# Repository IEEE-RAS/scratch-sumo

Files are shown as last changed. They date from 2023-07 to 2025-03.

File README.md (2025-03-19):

# Scratch Sumo

O scratch sumo é um projeto educacional para ensino de pensamento computacional e robótica usando linguagem de programação em bloco, como implementado por ferramentas como Scratch ou Google Blockly.
Consiste em 2 robôs-sumô que serão programados pelos estudantes e competem entre si num jogo simplificado.

## Materiais

- 2x Arduino NANO
- 2x MT3806 Step-up
- 2x USB Micro LiIon BMS
- 4x N20 Motor Reduzido
- 2x HC-SR04 Sensor Ultrassonico
- 4x Sensor Obstáculo Reflexivo IR
- 2x Ponte H L9110s
- 2x Buck Converter LM2596

O chassis é confectionado em plástico (majoritariamente ABS) e produzido por impressão 3D.

## Snapshot

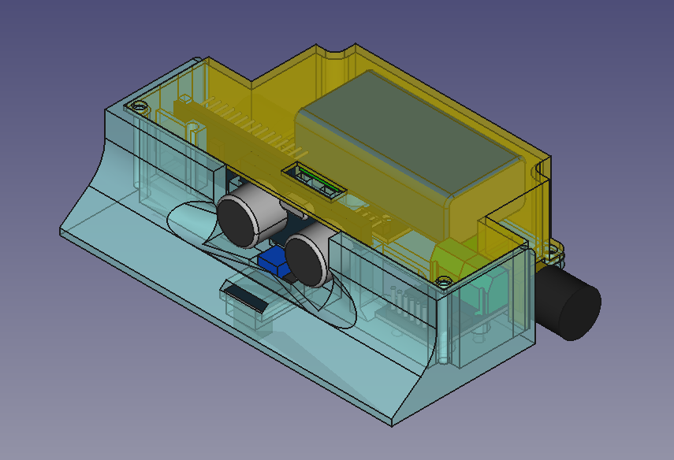
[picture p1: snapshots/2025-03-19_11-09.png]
Prototipo


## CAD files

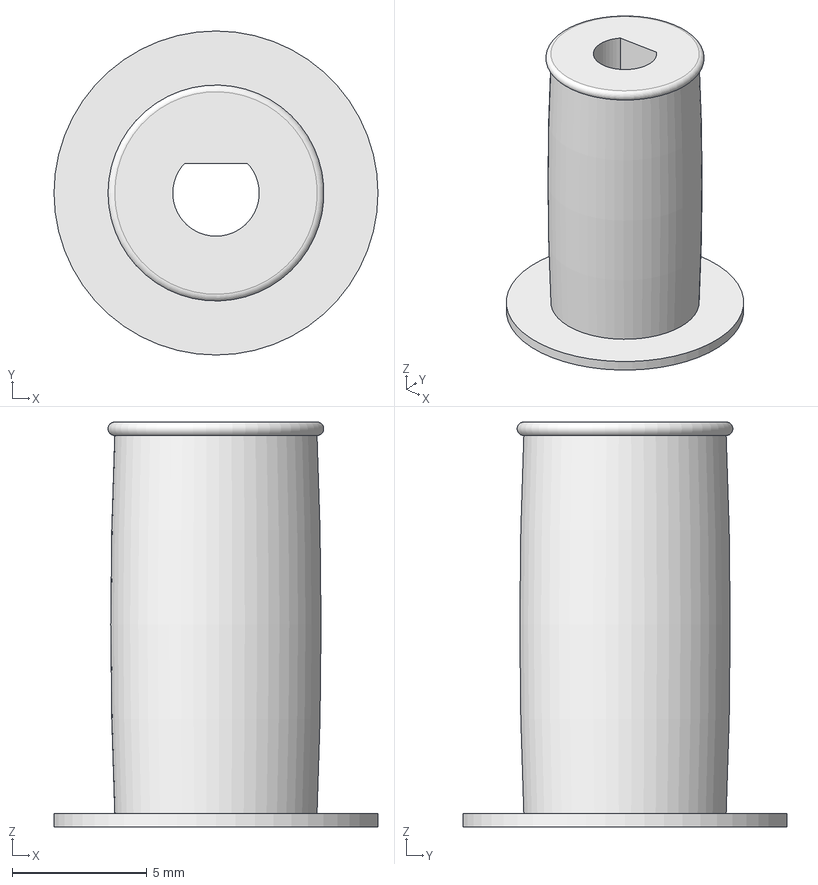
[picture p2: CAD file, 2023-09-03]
model/hub_roda.FCStd
12.0 x 12.0 x 15.0 mm

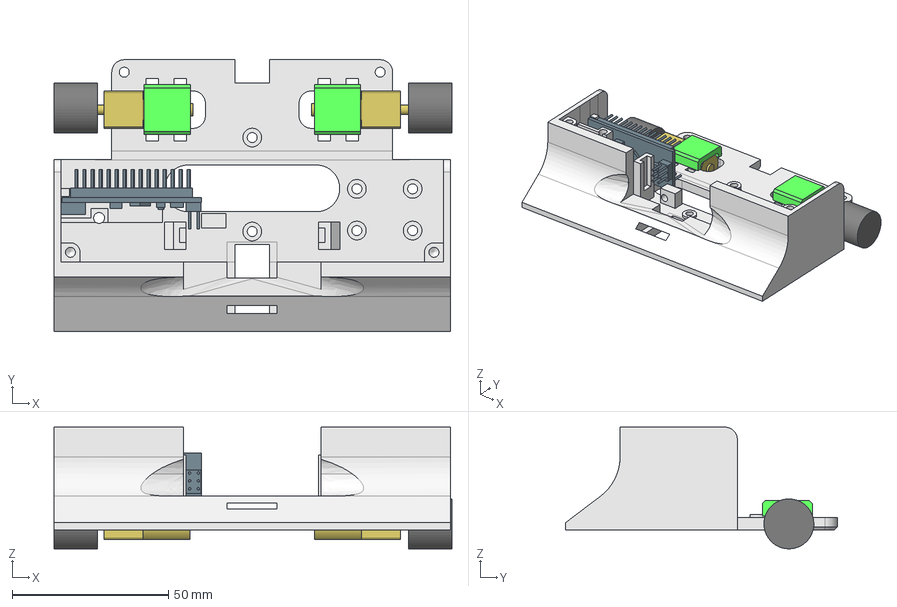
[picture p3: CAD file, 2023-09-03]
model/sumoV1.FCStd
127.5 x 87.0 x 39.0 mm
motor_support001
motor002
roda1
roda2
motor001
motor_support002
testbed001
nano

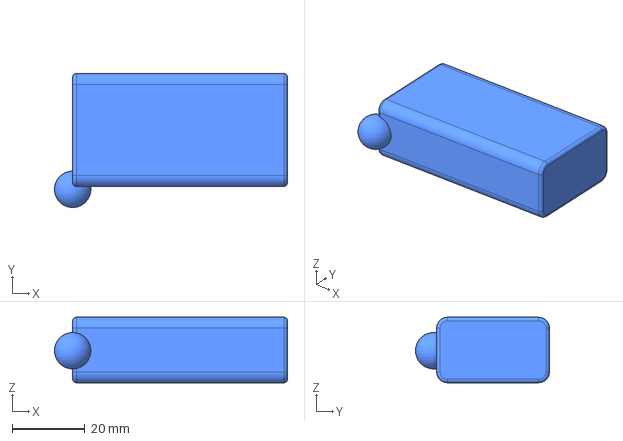
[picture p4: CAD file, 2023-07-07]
model/batteryPack.FCStd
64.0 x 36.8 x 18.0 mm

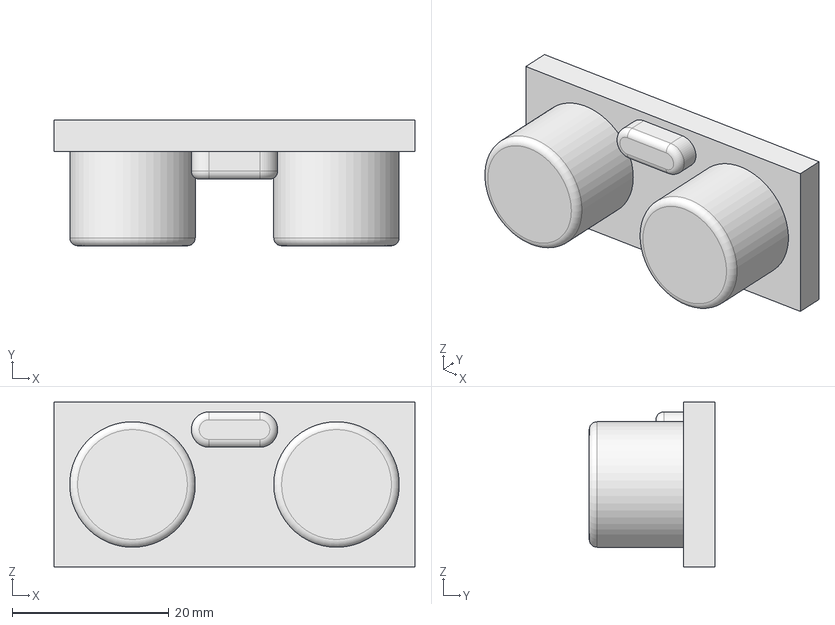
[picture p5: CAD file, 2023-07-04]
model/HC-SR04.FCStd
46.0 x 16.0 x 21.0 mm

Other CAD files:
model/HC-SR04-Body.stl

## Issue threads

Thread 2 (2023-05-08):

Modelagem Chassis

ShinJaca, 2023-05-08:
# Modelagem Chassis

O chassis do robo sumo será baseado no chassis desenvolvido para o seguidor de linha versão 2, feito em impressão 3D, é compacto e leve. Deverá também abrigar os sensores, baterias e placas de controle de forma "monolítica", além da pá frontal, característica de robôs sumô.

## Modificações necessárias

- Pá frontal: deve ter espaço para os sensores de ultrassom e infravermelho
- Espaço para roda: as rodas do robô sumô são maiores que as rodas do seguidor de linha, esse espaço deverá ser criado no layout do chassis.

ShinJaca, 2023-07-07:
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

Closed 2023-09-13.

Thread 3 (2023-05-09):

Teste de Baterias

Fernanda-Marinho, 2023-05-09:
3 baterias foram testadas:

- Uma pegou 3.8V, abaixou pra 3.7 e manteve
- Uma pegou 3.8V, abaixou pra 3.6, não acho que está mto boa
- Outra carregou bastante (não esperei o carregador apitar), mas pegou 3.9V

* Temos que ver se o carregador é programável.

victorcsar, 2023-05-11:
+2 baterias testadas:

- As duas vermelhas não passaram de 4.1V
- Ao retirar as duas descarregaram bem rápido e estabilizaram em 3.8

- Temos que verificar novamente se todas estão segurando a carga.

victorcsar, 2023-05-11:
Ainda tem mais de 15 baterias para testar, é o tempo de carregamento esta em torno de 64 min para cada. Nesse ritmo não sera possível testar todas no período de uma semana.

victorcsar, 2023-05-11:
seria interessante utilizar o seguidor de linha para verificar como será o comportamento das baterias ja carregadas, ou utilizar outro robô que esteja funcionando.

victorcsar, 2023-05-11:
[](https://www.youtube.com/watch?v=21b8qLPA_-M&ab_channel=JALASCKARC)

Video de como carregar as baterias, como o carregador é um pouco de ferente, tive que converter v para mah. As baterias pegam 3.6v segundo pesquisei, então aumentei no carregador para 3600 mah. Irei carregar uma para ve se muda alguma coisa.

Fernanda-Marinho, 2023-05-11:
Mais uma bateria foi carregada hoje (11/05), ficou com 3.9V

Fernanda-Marinho, 2023-05-11:
Mais uma bateria carrregada, com 3.8V. Ao todo, hj (11/05) temos 8 baterias carregadas: todas entre 3.6 e 3.9 V

Fernanda-Marinho, 2023-05-15:
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

Essa bateria tá marcando 3.7V, mas durante o carregamento esquentou muito, tirei com 2h de carregamento.
O carregador tá apitando bateria baixa pra as baterias com 2.0V e 2.3V
Ele foi programado pra só carregar acima de 2.4V?

Fernanda-Marinho, 2023-05-15:
Conferi a bateria que estava esquentando, já ta fria porém baixou de 4.0V para 3.8V
Mais duas baterias (das cinzas) foram carregadas (sem superaquecimento) e ficaram em 4.0V

Fernanda-Marinho, 2023-05-16:
Ao todo, temos 15 baterias  carregadas: entre 3.6V e 4.0V

victorcsar, 2023-05-17:
https://www.youtube.com/watch?v=uchFUiXPdQU&ab_channel=noteb00kpc
Esse video mostra como resolver o problema de low battery, tem uma opçao no carreador para chegar a bateria, deixa uns minutos depois da stop e coloca para carregar. O video carrega uma bateria de LIPo mas funciona para as de Lition.

victorcsar, 2023-05-17:
+1 bateria carregada, demorou 110 min e estava com 2v,  agora pegou 3.9V

Fernanda-Marinho, 2023-05-25:
Todas as baterias foram carregadas. Estamos começando a testar a duração delas no seguidor de linha

Fernanda-Marinho, 2023-05-25:
Uma bateria foi testada no seguidor de linha. Durou 40min porém foi de 3.8V para 3.7V
Eu acho que o seguidor de linha possa estar com mal contato ou algum bug. Um dos sensores do seguidor (S5) não ta funcionando

Fernanda-Marinho, 2023-05-26:
Precisa ver como funciona a função de descarregar a bateria. Pois muito provável que ela dê um valor em Mah e aí olhando quanto a bateria tem (de fábrica) dá pra ter uma noção de quantos por cento de carga ela tem. Se tiver uns 80% de carga ainda, ta boa.

Fernanda-Marinho, 2023-05-26:
https://pdf1.alldatasheet.com/datasheet-pdf/view/597041/PANASONICBATTERY/NCR18650.html (datasheet de uma das baterias testadas no seguidor de linha), vem com capacidade de fábrica de 2900mAh
Ela vai do max 4.2V (no carregamento)
E min de 2.5V (no descarregamento) pelo q eu entendi. Se tiver errado olhem o pdf e me corrijam

Closed 2023-07-04.

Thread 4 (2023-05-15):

Teste dos sensores

Fernanda-Marinho, 2023-05-15:

Fernanda-Marinho, 2023-05-15:
Quais sensores serão testados? Precisamos separar esses sensores e deixar reservado. Até o momento eu só sei do sonar.

ShinJaca, 2023-07-12:
Sensores:
- [x] TCRT5000 sensor IR
- [ ] HC-SR04 sensor ultrassom

ShinJaca, 2023-07-13:
## Atualização

Um teste mais extenso com 2 sensores ultrassonicos realizados um contra o outro demonstrou que os sensores afastados a partir de cerca de 15cm interferem e corrompem as medidas um do outro

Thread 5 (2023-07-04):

Função Blockly@rduino

ShinJaca, 2023-07-04:
# Funções a implementar

**Movimento**:
- andar pra frente
- andar pra tras
- andar pra frente e esquerda
- andar à frente e direita
- andar à tras esquerda
- andar à tras direta

**Sensores**:
- Ler distância sensor ultrassom
- ler detecção de borda (sensor IR)

Fernanda-Marinho, 2023-07-11:
Documentação blockly -> https://developers.google.com/blockly?hl=pt-br&authuser=0
Projeto blockly@rduino ->
Código-fonte (a ideia é fazer um fork e ir modificando conforme nossas necessidades) -> https://github.com/technologiescollege/Blockly-at-rduino

Fernanda-Marinho, 2023-07-11:
Achei o código que gera o "Blockly.Arduino", está dentro da pasta "generation". Lá ele contém as funções que traduz o que é Blockly para arduino.
Tem funções também que adiciona os includes, incializa código e verifica variáveis.

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

ShinJaca, 2023-07-20:
## Rodando localmente

Para rodar localmente usei o método de container com docker, para tanto é interessante criar o arquivo Dockerfile no raiz do repositório do Blockly@rduino contendo a diretiva:
```dockerfile
FROM httpd:2.4
```
em seguida, estando no repositório, construir a imagem ( necessário toda vez que algumas alterações são feitas ):
```bash
docker build -t apache2-server .
```
ao finalizar, iniciar um container com a imagem criada:
```bash
docker run -dit --name blocklyarduino -p 8080:80 --mount type=bind,src=.,dst=/usr/local/apache2/htdocs apache2-server
```
e acessando a aplicação pelo navegador através do endereço localhost:8080 ( nesse caso a porta encaminhada foi 8080, mas pode ser a de preferência ).

ShinJaca, 2023-07-20:
## Criando uma biblioteca

A aplicação usa basicamente 5 arquivos para configurar uma biblioteca:
- toolbox/toolbox_arduino_1.xml ( ou outro nível )
- lang/pt-br.js ( e outras traduções )
- blocks/arduino_resume.js ( contém a chamada para as definições de bloco )
- blocks/fabricante/fabricante.js ( substituindo o fabricante pelo nome da biblioteca, definições de bloco )
- generators/arduino_resume.js ( chamada para as definições do gerador de codigo )
- generators/fabricante.js (definições dos geradores )

### Toolbox

A toolbox, ou caixa de ferramentas agrupa os blocos disponíveis para o projeto, nesse caso é pensado para servir de agrupamento por nível de dificuldade, mais ou menos abstrato.
Aqui são listados os blocos que aparecem para o usuário:
```xml
<category name="CAT_NOME" colour="#6D0194">
	<block type="fabricante_nome_do_bloco"></block>
        <block type="fabricante_outro_bloco"></block>
</category>
```

### Traduções

Para que a biblioteca apareça na listagem do nível selecionado, uma tradução para ela deve ser criada nos arquivos de traduções da pasta `lang/BlocklyArduino_blocks`, numa propriedade específica para a biblioteca (categoria), como segue:
```js
Blockly.Msg.CAT_NOME = "Nome da Biblioteca";
```
### TODO
- resumes
- blocks
- generators

ShinJaca, 2023-07-20:
# Funções de teste

Três funções de teste foram implementadas `moveFrente`, `moveTras` e `parar`, para fazer funcionar, é necessário mesclar os arquivos de configuração e copiar os arquivos de definição de blocos e gerador na sua copia do Blockly@rduino.

Closed 2023-08-07.

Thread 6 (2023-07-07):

Funções Arduino

ShinJaca, 2023-07-07:
# Funções Arduino

Desenvolvimento das funções necessárias para funcionamento do robô ( codigo em linguagem para o arduino )

**Funções de movimento:**
- seguir em frente
- seguir à tras
- à frente e esquerda
- à frente e direita
- tras e esquerda
- tras e direita
- parar

**Funções de sensores**:
- ler sensor de distância ( Ultrassom )
- ler sensores de borda ( IR )

ShinJaca, 2023-07-13:
## Modulo ponte H
O nosso modulo de ponte H não provém pino de enable, sendo necessário modular um dos pinos de controle de direção para produzir o efeito de controle de rotação dos motores, assim também economizando 2 pinos. mas exigindo agora que os pinos de controle sejam todos pinos com PWM 🥲.

Closed 2023-08-17.

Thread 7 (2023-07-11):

Impressão prototipo

ShinJaca, 2023-07-11:
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

ShinJaca, 2023-07-11:
Primeiro protótipo:
- pinos posicionamento para driver de motor
- pinos posicionamento para sensores IR
- suporte para sensor ultrassom
- slot para sensor ultrassom
- slots para sensores IR

Closed 2023-07-11.

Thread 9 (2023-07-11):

Testes de Movimento

ShinJaca, 2023-07-11:

ShinJaca, 2023-07-20:
## Movimentos
Foram realizados testes de movimento com avanço, retrocesso e curvas, mas aparentemente existe um problema com constância de um dos motores, aparentemente a frequência de PWM do pino escolhido pode estar influenciando na rotação e causando instabilidades.

Closed 2023-08-07.

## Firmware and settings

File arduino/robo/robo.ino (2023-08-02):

// Código de referência em: https://blog.arduinoomega.com/robo-autonomo-basico-com-sensor-ultrassonico-hc-sr04/

// Bibliotecas necessárias
#include <NewPing.h> // https://bitbucket.org/teckel12/arduino-new-ping/wiki/Home#!newping-arduino-library-for-arduino

// Definição dos pinos dos motores (PWM) // https://lobodarobotica.com/blog/arduino-nano-pinout/
#define MOTOR_A_IN1 3 // D3
#define MOTOR_A_IN2 9 // D5
#define MOTOR_B_IN3 10 // D6
#define MOTOR_B_IN4 11 // D9

// Definição do pino do sensor infravermelho (Analógico)
// #define SENSOR_IR 19 // A0
#define SENSOR_IR_FRENTE 5
#define SENSOR_IR_TRAS 6

// Definição dos pinos do sensor ultrassônico HC-SR04 (Digitais)
#define TRIGGER_PIN 7 // D7
#define ECHO_PIN 8 // D8

// Velocidades dos motores
#define VELOCIDADE_MAXIMA = 255;
#define VELOCIDADE_GIRO = 200;

// Configuração do sensor ultrassônico
NewPing sonar(TRIGGER_PIN, ECHO_PIN);

// Função para mover o robô para frente
void moverParaFrente(int velocidade) {
  analogWrite(MOTOR_A_IN1, velocidade);
  analogWrite(MOTOR_A_IN2, 0);
  analogWrite(MOTOR_B_IN3, velocidade);
  analogWrite(MOTOR_B_IN4, 0);
}

// Função para mover o robô para trás
void moverParaTras(int velocidade) {
  analogWrite(MOTOR_A_IN1, 0);
  analogWrite(MOTOR_A_IN2, velocidade);
  analogWrite(MOTOR_B_IN3, 0);
  analogWrite(MOTOR_B_IN4, velocidade);
}

// Função para parar o robô
void parar() {
  digitalWrite(MOTOR_A_IN1, 1);
  digitalWrite(MOTOR_A_IN2, 1);
  digitalWrite(MOTOR_B_IN3, 1);
  digitalWrite(MOTOR_B_IN4, 1);
  delay(100);
  digitalWrite(MOTOR_A_IN1, 0);
  digitalWrite(MOTOR_A_IN2, 0);
  digitalWrite(MOTOR_B_IN3, 0);
  digitalWrite(MOTOR_B_IN4, 0);
}

// Função para girar o robô para a esquerda
void girarEsquerda(int velocidade) {
  analogWrite(MOTOR_A_IN1, 0);
  analogWrite(MOTOR_A_IN2, velocidade);
  analogWrite(MOTOR_B_IN3, velocidade);
  analogWrite(MOTOR_B_IN4, 0);
}

// Função para girar o robô para a direita
void girarDireita(int velocidade) {
  analogWrite(MOTOR_A_IN1, velocidade);
  analogWrite(MOTOR_A_IN2, 0);
  analogWrite(MOTOR_B_IN3, 0);
  analogWrite(MOTOR_B_IN4, velocidade);
}

// Função para mover o robô à frente e esquerda (utilizando apenas rotação dos motores)
void moverFrenteEsquerda() {
  analogWrite(MOTOR_A_IN1, 0);
  analogWrite(MOTOR_A_IN2, VELOCIDADE_GIRO);
  analogWrite(MOTOR_B_IN3, VELOCIDADE_MAXIMA);
  analogWrite(MOTOR_B_IN4, 0);
  delay(500);  // Ajuste esse tempo conforme necessário para a curva
  parar();
}

// Função para mover o robô à frente e direita (utilizando apenas rotação dos motores)
void moverFrenteDireita() {
  analogWrite(MOTOR_A_IN1, VELOCIDADE_MAXIMA);
  analogWrite(MOTOR_A_IN2, 0);
  analogWrite(MOTOR_B_IN3, 0);
  analogWrite(MOTOR_B_IN4, VELOCIDADE_GIRO);
  delay(500);  // Ajuste esse tempo conforme necessário para a curva
  parar();
}

// Função para mover o robô para trás e esquerda (utilizando apenas rotação dos motores)
void moverTrasEsquerda() {
  analogWrite(MOTOR_A_IN1, VELOCIDADE_GIRO);
  analogWrite(MOTOR_A_IN2, 0);
  analogWrite(MOTOR_B_IN3, 0);
  analogWrite(MOTOR_B_IN4, VELOCIDADE_MAXIMA);
  delay(500);  // Ajuste esse tempo conforme necessário para a curva
  parar();
}

// Função para mover o robô para trás e direita (utilizando apenas rotação dos motores)
void moverTrasDireita() {
  analogWrite(MOTOR_A_IN1, 0);
  analogWrite(MOTOR_A_IN2, VELOCIDADE_MAXIMA);
  analogWrite(MOTOR_B_IN3, VELOCIDADE_GIRO);
  analogWrite(MOTOR_B_IN4, 0);
  delay(500);  // Ajuste esse tempo conforme necessário para a curva
  parar();
}

void setup() {
  // Configuração dos pinos dos motores e do sensor infravermelho
  pinMode(MOTOR_A_IN1, OUTPUT);
  pinMode(MOTOR_A_IN2, OUTPUT);
  pinMode(MOTOR_B_IN3, OUTPUT);
  pinMode(MOTOR_B_IN4, OUTPUT);
  pinMode(SENSOR_IR_FRENTE, INPUT);
  pinMode(SENSOR_IR_TRAS, INPUT);

  Serial.begin(9600);
}

void loop() {
  // Verifica se está na borda (superfície branca) usando o sensor infravermelho
  bool naBorda = digitalRead(SENSOR_IR);
  // Verifica a distância medida pelo sensor ultrassônico
  unsigned int distanciaFrente = sonar.ping_cm();
  Serial.print("Distancia frente: ");
  Serial.print(distanciaFrente);
  Serial.println(" cm");

  // Implementar lógica abaixo
}

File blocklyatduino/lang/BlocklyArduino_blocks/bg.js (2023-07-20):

'use strict';

goog.provide('Blockly.Msg.bg');

goog.require('Blockly.Msg');

Blockly.Msg.ARRAY_CREATE_EMPTY_TITLE = 'празно!';
Blockly.Msg.tab_create="създай блок елемент за масив %1'";
Blockly.Msg.tab_create_fix="създай блок 'задай елемент в масив %1 до'";
Blockly.Msg.ARRAY_CREATE_WITH="задай с/със";
Blockly.Msg.ARRAY_taille="размер";
Blockly.Msg.ARRAY_contenu="съдържа";
Blockly.Msg.ARRAY_dim="с размер ";
Blockly.Msg.ARRAY_index="индекс";
Blockly.Msg._AT= "до";
Blockly.Msg.ARRAY_CREATE_WITH = "създаден с";
Blockly.Msg.ARRAY_CREATE_WITH_CONTAINER_TITLE_ADD = "масив";
Blockly.Msg.ARRAY_CREATE_WITH_CONTAINER_TOOLTIP = "Добави, премахни или пренареди секциите, за да конфигурираш отново този масив.";
Blockly.Msg.ARRAY_CREATE_WITH_HELPURL = "";
Blockly.Msg.ARRAY_CREATE_WITH_INPUT_WITH = "масив";
Blockly.Msg.ARRAY_CREATE_WITH_ITEM_TITLE = "елемент";
Blockly.Msg.ARRAY_CREATE_WITH_ITEM_TOOLTIP = "Добави елемент към масива.";
Blockly.Msg.ARRAY_CREATE_WITH_TOOLTIP = "Създай масив с произволен брой елементи.";
Blockly.Msg.ARRAY_GETINDEX_AT = "вземи индекс";
Blockly.Msg.ARRAY_GETINDEX_AT1 = "вземи индекс";
Blockly.Msg.ARRAY_GETINDEX_AT2 = "индекс";
Blockly.Msg.ARRAY_GETINDEX_HELPURL = "";
Blockly.Msg.ARRAY_GETINDEX_ITEM = "в Масив";
Blockly.Msg.ARRAY_GETINDEX_TOOLTIP = "";
Blockly.Msg.ARRAY_GETINDEX_TOOLTIP1="връща стойността, запазена в списъка или таблицата";
Blockly.Msg.ARRAY_GETINDEX_TOOLTIP2="създава списък или таблица от избрания тип";
Blockly.Msg.ARRAY_GETINDEX_TOOLTIP3="задава един (или повече) елемент(и) в списъка или таблицата на определената(ите) стойност(и)";
Blockly.Msg.ARRAY_CREATE = "дефиниране ";
Blockly.Msg.ARRAY_TAILLE = "размер";
Blockly.Msg.ARRAY_CONTIENT = "с";
Blockly.Msg.ARRAY_LIST = "списък";
Blockly.Msg.ARRAY_ARRAY = "масив";
Blockly.Msg.ARRAY_fixe = "промени елемент на позиция";
Blockly.Msg.ARRAY_DECLARE_NAME = "създай масив";
Blockly.Msg.ARRAY_DECLARE_TYPE = "тип";
Blockly.Msg.ARRAY_DECLARE_SIZE = "брой елементи";
Blockly.Msg.ARRAY_DECLARE_TOOLTIP = "създай масив от конкретен тип и брой елементи";
Blockly.Msg.ARRAY_MODIFY_INDICE = "задай елеемнт nb";
Blockly.Msg.ARRAY_MODIFY_NAME = "в масив";
Blockly.Msg.ARRAY_MODIFY_VALUE = "стойност";
Blockly.Msg.ARRAY_MODIFY_TOOLTIP = "задава конкретна стойност на елемент от масива (Array)";

//ESK 6/13/2015 SWITCH CASE
Blockly.Msg.CONTROLS_SWITCH_CASEBREAK_TOOLTIP = "Добавя условие към блока 'в случай' (case)";
Blockly.Msg.CONTROLS_SWITCH_DEFAULT_TOOLTIP = "Добавете окончателно условие за прихващане към блока 'ако' (if).";
Blockly.Msg.CONTROLS_SWITCH_HELPURL = "https://en.wikipedia.org/wiki/Switch_statement";
Blockly.Msg.CONTROLS_SWITCH_SWITCH_TOOLTIP = "Добави, премахни или пренареди секциите, за да преконфигурираш този, 'ако' (if) блок.";
Blockly.Msg.CONTROLS_SWITCH_VAR_TITLE = "Превключи (";
Blockly.Msg.CONTROLS_SWITCH_VAR_TAIL = ")";
Blockly.Msg.CONTROLS_SWITCH_MSG_DEFAULT = "по подразбиране (default)";
Blockly.Msg.CONTROLS_SWITCH_MSG_CASEBREAK = "в случай (case)";
Blockly.Msg.CONTROLS_SWITCH_MSG_SWITCHVAR = "Превключи (var)";
Blockly.Msg.CONTROLS_SWITCH_MSG_DO = "направи";
Blockly.Msg.CONTROLS_SWITCH_TOOLTIP_1 = "Ако стойността е вярна (true), изпълни израза.";
Blockly.Msg.CONTROLS_SWITCH_TOOLTIP_2 = "Ако стойността е вярна (true), изпълни първия блок от израза. В противен случай изпълни втория блок от израза.";
Blockly.Msg.CONTROLS_SWITCH_TOOLTIP_3 = "Ако първата стойност е вярна (true), изпълни първия блок от израза. В противен случай, ако втората стойност е вярна (true), изпълни втория блок.";
Blockly.Msg.CONTROLS_SWITCH_TOOLTIP_4 = "Ако първата стойност е вярна (true), изпълни първия блок от израза. В противен случай, ако втората стойност е вярна (true), изпълни втория блок. Ако нито една от стойностите е вярна (true), изпълни последния блок от израза.";
Blockly.Msg.CONTROLS_SWITCH_VAR_TOOLTIP = "Влачете отляво тук, за да добавите";
Blockly.Msg.CONTROLS_SWITCH_CASEBREAK_TOOLTIP = "Добавете допълнителен 'в случай прекъсни направи' (case break do)";
Blockly.Msg.CONTROLS_SWITCH_DEFAULT_TOOLTIP ="Добави окончателно прихващане (default) по избор";

Blockly.Msg.TEXT_CHAR_TOOLTIP = "символна стойност, която заема 1 байт памет";
Blockly.Msg.TEXT_CHAR_HELPURL = "https://www.arduino.cc/reference/en/language/variables/data-types/string/";
Blockly.Msg.TEXT_COMPARE_STRING_HELPURL = "";
Blockly.Msg.TEXT_COMPARE_STRING_TEXT = "Сравнение на двете вериги: ";
Blockly.Msg.TEXT_COMPARE_STRING_TEXT2 = " = ";
Blockly.Msg.TEXT_COMPARE_STRING_TOOLTIP = "Показва дали двата низа са идентични или не.";


//july 9th function from JP Fontaine workspace
Blockly.Msg.PROCEDURES_DEFRETURN_FUNCTION = "за функция";
Blockly.Msg.PROCEDURES_DEFRETURN_TYPE = "тип";

Blockly.Msg.VARIABLES_AS = "като";
Blockly.Msg.VARIABLES_SET_CONST = "константа";
Blockly.Msg.VARIABLES_SET_CONST_AT = "задай";
Blockly.Msg.VARIABLES_SET_CONST_TOOLTIP = "set a variable to non modifiable value";
Blockly.Msg.VARIABLES_SET_CONST_HELPURL = "https://www.arduino.cc/reference/en/language/variables/variable-scope-qualifiers/const/";
Blockly.Msg.ARD_TYPE_ARRAY = "Масив (Array)";
Blockly.Msg.ARD_TYPE_BOOL = "Булева (Boolean)";
Blockly.Msg.ARD_TYPE_CHAR = "Буква (Character)";
Blockly.Msg.ARD_TYPE_ARRAY_CHAR = "Буква Масив (Array of character)";
Blockly.Msg.ARD_TYPE_CHILDBLOCKMISSING = "ChildBlockMissing";
Blockly.Msg.ARD_TYPE_DECIMAL = "Десетичен (Decimal)";
Blockly.Msg.ARD_TYPE_LONG = "Голямо число (Large Number)";
Blockly.Msg.ARD_TYPE_NULL = "Нула (Null)";
Blockly.Msg.ARD_TYPE_NUMBER = "Число (Number)";
Blockly.Msg.ARD_TYPE_SHORT = "Кратко число (Short Number (byte))";
Blockly.Msg.ARD_TYPE_TEXT = "Текст (Text)";
Blockly.Msg.ARD_TYPE_UNDEF = "Неопределен (Undefined)";
Blockly.Msg.ARD_TYPE_UNS_NUMBER = "Неопределено число (Unsigned number)";
Blockly.Msg.ARD_TYPE_UNS_LONG = "Неопределено голямо число (Unsigned Long Number)";
Blockly.Msg.ARD_TYPE_VOLATILE = "Непостоянно цяло число (Volatile integer)";

//**********************************categories***********************************************
//**********************************categories***********************************************
//**********************************categories***********************************************

Blockly.Msg.CAT_LOOPS = "Цикли";
Blockly.Msg.CAT_LOGIC = "Логика";
Blockly.Msg.CAT_IF = "Ако (If)";
Blockly.Msg.CAT_BOOL = "Булеви";
Blockly.Msg.CAT_MATH = "Математика";
Blockly.Msg.CAT_TEXT = "Текст";
Blockly.Msg.CAT_LIST = "Списъци";
Blockly.Msg.CAT_ARRAY = "Масиви";
Blockly.Msg.CAT_COLOR = "Цвят";
Blockly.Msg.CAT_VARIABLES = "Променливи";
Blockly.Msg.CAT_FUNCTIONS = "Функции";
Blockly.Msg.CAT_ARDUINO = "Arduino";
Blockly.Msg.CAT_ARDUINO_IN = "Вход";
Blockly.Msg.CAT_ARDUINO_OUT = "Изход";
Blockly.Msg.CAT_ARDUINO_CONVERSION = "Конвертиране";
Blockly.Msg.CAT_ARDUINO_TIME = "Време";
Blockly.Msg.CAT_ARDUINO_COMM_SERIAL = "Серийна комуникация ";
Blockly.Msg.CAT_ARDUINO_COMM_SOFTSERIAL = "Софтсериал библиотека";
Blockly.Msg.CAT_ARDUINO_SERVO = "Серво мотор";
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

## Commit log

2023-06-02 modelo sensor HC-SR04
    [HC-SR04-Body.stl, HC-SR04.FCStd]
2023-07-04 Modelo preliminar
    [HC-SR04.FCStd, sumoV1.FCStd]
2023-07-07 update ir sensor position
    [batteryPack.FCStd, sumoV1.FCStd]
2023-07-20 Arquivos para o Blockly@rduino
2023-07-25 Movt. diagonais apenas com rotação, 4 pwm do motor
2023-07-25 testes com o sumo e motor
2023-08-02 implementação de freio e repinagem
2023-08-03 cobertura do robô
    [sumoV1.FCStd]
2023-08-07 implementação de todas as funções de movimento
2023-08-07 função de leitura de sonar (cm)
2023-08-07 leitura de sensores IR
2023-08-09 parafusos cover frontaç
    [sumoV1.FCStd]
2023-08-15 Parafusos de fixação
    [sumoV1.FCStd]
2023-09-03 parafusos no chassis e roda
    [hub_roda.FCStd, sumoV1.FCStd]
